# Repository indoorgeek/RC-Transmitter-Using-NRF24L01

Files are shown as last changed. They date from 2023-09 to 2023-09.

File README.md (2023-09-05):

# RC Transmitter Using NRF24L01
 <br/>
When I was a child, I was fascinated by drones and always wanted to have one. But they were not so common those days and quite expensive too. My brother once got a small cheap RC helicopter and we used to fly it almost every day till it's battery completely died. We were not competent enough to open it up and change the battery. So, that was it, my first and only experience with RC! But now, with a sound knowledge of electronics and lots of resources available on the internet, I want to build my own drone. Also, I am into photography as well and so I am planning to mount a camera onto it to get some cool shots from the above! But building a drone is one thing and flying it properly without crashing is totally a different thing. That's why I decided to build a small drone using Arduino to get a feel of the controls.
# The Plan
 <br/>
I did some research on the internet since I am very new to the RC world. I came across [Electronoob's](https://www.youtube.com/@ELECTRONOOBS) YouTube channel which has some great content on this topic. He has built a small drone using brushed DC motors which in fact inspired me to build my own. I will be following his build and making changes as per my needs.<br/>

My plan is to build the drone in two parts. First I will make the transmitter and then the drone itself which will have the receiver built-in.<br/>

# PCB Design
<p float="center">
  
   
</p> 

I got my PCBs manufactured from [JLCPCB!](https://jlcpcb.com/DAA). Get your PCBs beautifully fabricated from JLCPCB for just 2$!

The most important and necessary controls are throttle, yaw, roll, and pitch. These analog inputs will be provided by two 2-axis joysticks. I have added two 10k potentiometers to which other helpful controls like throttle trim, pitch trim, etc can be assigned. I have also used two switches to provide digital inputs which then can be used to toggle between different flight modes. For beginners like me, these inputs are sufficient to get started.

Arduino will be the brains of this build. You could use almost any Arduino development board like Nano. But to keep everything neat and tidy I decided to use the ATMega328P microcontroller directly on the PCB. First, I drew the outline of the shape of the controller in Fusion 360. I made sure it feels comfortable in hand and all the controls are easily accessible. Once I was happy with the shape, I imported it as DWG file in Altium Designer. I then made the connections as usual. I was about to call it a day when it struck me that I could design yet another PCB to go on top of the other one as a front cover. It would be more comfortable to hold too. Also, why not make a simple PCB art to make it look cool since doing this is a piece of cake in Altium Designer. Click here to get a free trial of Altium Designer. I asked my wife who is an artist ([@swirls_of_solace](https://www.instagram.com/swirls_of_solace/)) to create something which will look good on it and she didn't disappoint!

I have provided a female header connector to program the microcontroller using the RS232 FTDI breakout board. To be able to program it using the Arduino IDE, the bootloader should be burned onto it prior to soldering on PCB. I had salvaged the microcontroller from a Nano so it was already present. You can find many tutorials on the internet for burning the bootloader.

The most important and tricky part of this project is to power the NRF24 module correctly. The module works on 3.3V and can lead to current surges when powering ON or while transmitting the data. So, appropriate capacitors should be connected across the power rails. While testing the circuit I had used an AMS1117 3.3V power adapter board specially made for NRF24 modules and it had worked flawlessly. So I just recreated that circuit for this project.

# Assembly
 <br/>
I used the same outline, which I had used to make the PCB, to create the body around it. The body is again divided into two parts. The battery will be placed between the bottom PCB and the body. I have used threaded inserts for the screws. Everything will go together as shown in the picture and be held together by 4 M3 screws.

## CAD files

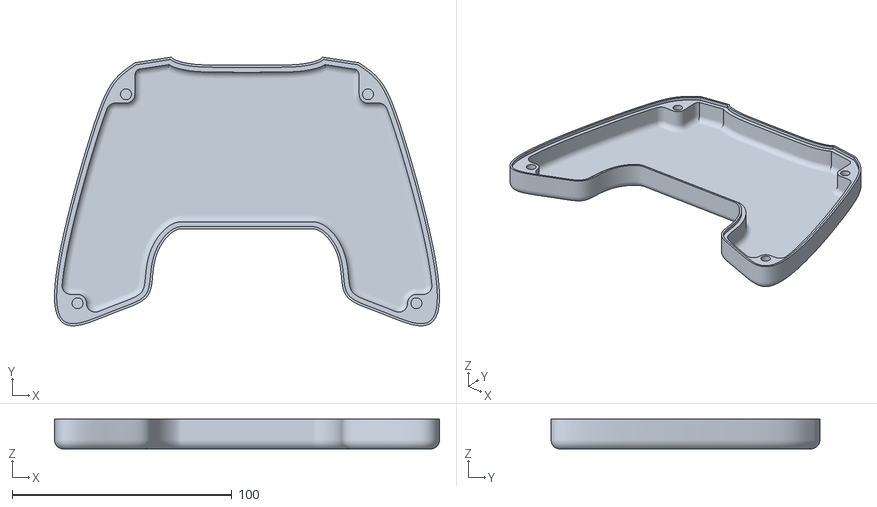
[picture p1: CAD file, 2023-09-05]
3D/BottomBody.stl
175.0 x 122.2 x 13.6

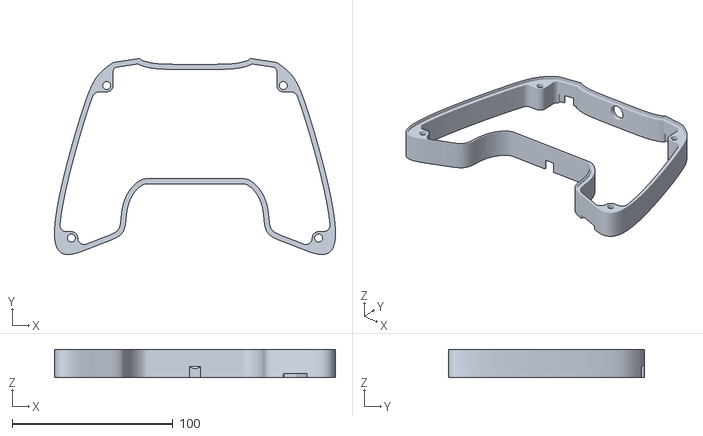
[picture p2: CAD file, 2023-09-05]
3D/TopBody.stl
175.0 x 122.2 x 17.6

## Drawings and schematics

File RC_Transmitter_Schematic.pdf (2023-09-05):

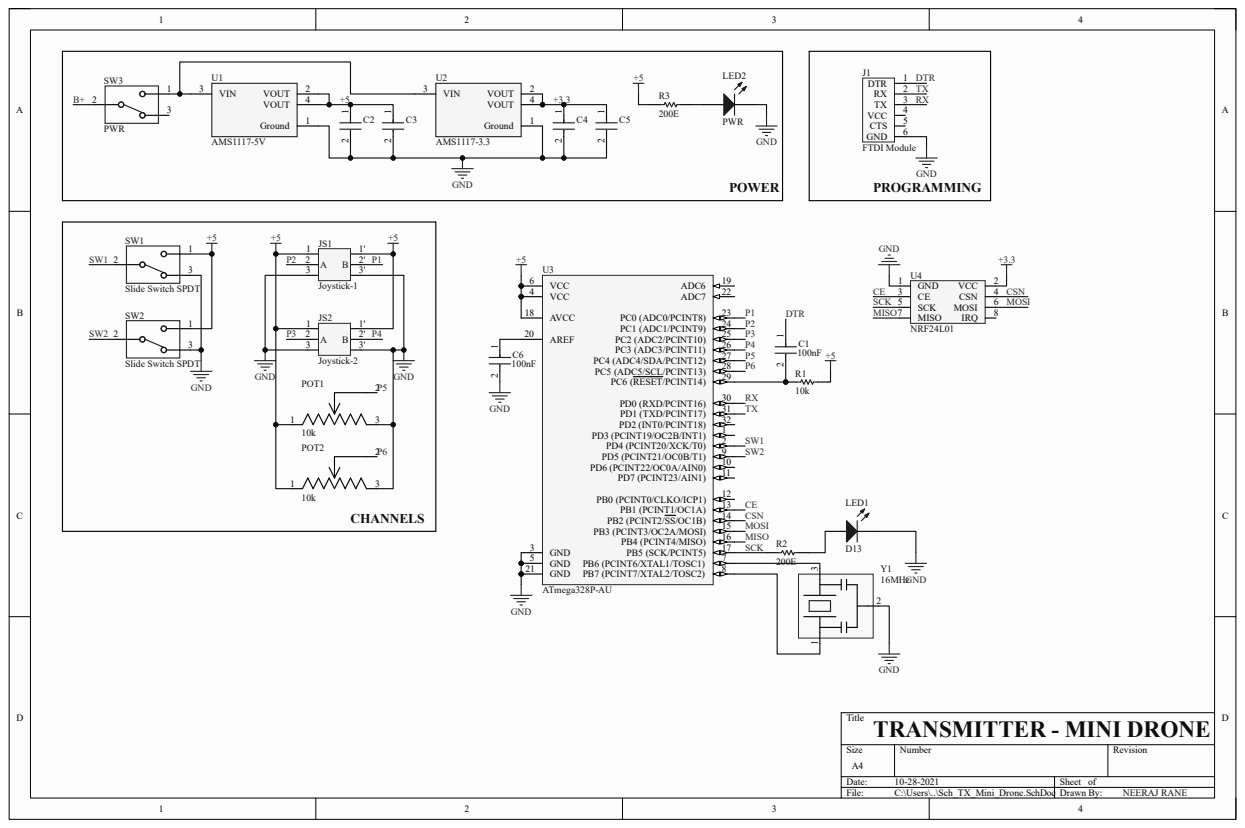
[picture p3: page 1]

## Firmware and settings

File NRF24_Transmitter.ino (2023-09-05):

/*A basic 4 channel transmitter using the nRF24L01 module.*/
/* Like, share and subscribe, ELECTRONOOBS */
/* http://www.youtube/c/electronoobs */

/* First we include the libraries. Download it from 
   my webpage if you donw have the NRF24 library */
 
#include <SPI.h>
#include <nRF24L01.h>
#include <RF24.h>

/*Create a unique pipe out. The receiver has to 
  wear the same unique code*/
  
const uint64_t pipeOut = 0xE8E8F0F0E1LL;

RF24 radio(9, 10); // select  CSN  pin

// The sizeof this struct should not exceed 32 bytes
// This gives us up to 32 8 bits channals
struct MyData {
  byte throttle;
  byte yaw;
  byte pitch;
  byte roll;
  byte AUX1;
  byte AUX2;
};

MyData data;

void resetData() 
{
  //This are the start values of each channal
  // Throttle is 0 in order to stop the motors
  //127 is the middle value of the 10ADC.
    
  data.throttle = 0;
  data.yaw = 127;
  data.pitch = 127;
  data.roll = 127;
  data.AUX1 = 0;
  data.AUX2 = 0;
}

void setup()
{
  //Start everything up
  radio.begin();
  radio.setAutoAck(false);
  radio.setDataRate(RF24_250KBPS);
  radio.openWritingPipe(pipeOut);
  resetData();
}

/**************************************************/

// Returns a corrected value for a joystick position that takes into account
// the values of the outer extents and the middle of the joystick range.
int mapJoystickValues(int val, int lower, int middle, int upper, bool reverse)
{
  val = constrain(val, lower, upper);
  if ( val < middle )
    val = map(val, lower, middle, 0, 128);
  else
    val = map(val, middle, upper, 128, 255);
  return ( reverse ? 255 - val : val );
}

void loop()
{
  // The calibration numbers used here should be measured 
  // for your joysticks till they send the correct values.
  data.throttle = mapJoystickValues( analogRead(A0), 0, 523, 1023, true );
  data.yaw      = mapJoystickValues( analogRead(A1),  0, 512, 1023, true );
  data.pitch    = mapJoystickValues( analogRead(A3), 0, 516, 1023, true );
  data.roll     = mapJoystickValues( analogRead(A2), 0, 524, 1023, true );
  data.AUX1     = digitalRead(4);
  data.AUX2     = digitalRead(5);

  radio.write(&data, sizeof(MyData));
}
